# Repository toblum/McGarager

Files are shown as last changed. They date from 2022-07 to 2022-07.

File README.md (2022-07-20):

# McGarager v2
Simple MQTT garage door opener with endstop detection (reed sensor)

This is a rewrite of the initial McGarager firmware. It fits to the McGarager PCB.

It uses:
- The [prampec/IotWebConf@^3.2.1](https://github.com/prampec/IotWebConf) framework for easy setup, captive portal, config UI and OTA firmware upload.
- [knolleary/PubSubClient@^2.8](https://github.com/knolleary/pubsubclien) for MQTT communication
- [yiannisbourkelis/Uptime Librar@^1.0.0](https://github.com/YiannisBourkelis/Uptime-Library) for easy uptime display
- [Platformio](https://platformio.org/) for the build process.

Notes:
- No support for neopixel as of now.

Initial config values:
- AP SSID: McGarager / GaragerMc
- Config-UI credentials: admin / GaragerM
- Base MQTT topic: mc_garager

MQTT topics:
- #Base MQTT topic#/status: McGarager publishes JSON status messages to this topic when open/close inputs have changed of if trigged via command.
- #Base MQTT topic#/cmnd:   
  Topic that receives commands
    - Message "status": Trigger sending of status message.
    - Message "trigger": Make the relay close for 250 ms.

## PCB v1.0

- [Gerber files](assets/PCB/Gerber_PCB.zip)
- [BOM](assets/PCB/BOM_PCB_2022-07-20.csv)
- [Schematic](assets/PCB/Schematic_McGarager_2022-07-20.pdf)
- [Front](assets/PCB/PCB_PCB_2022-07-20_front.pdf)
- [Back](assets/PCB/PCB_PCB_2022-07-20_back.pdf)

Preview:
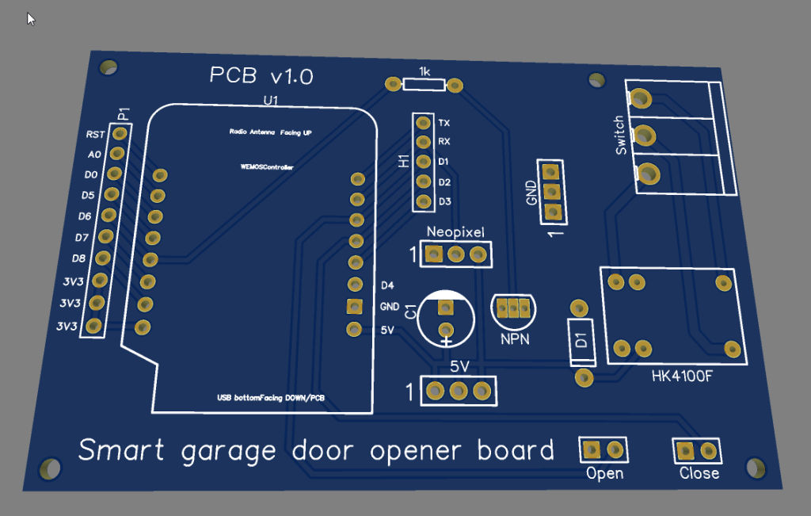
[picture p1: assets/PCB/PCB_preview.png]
PCB Preview


Front:
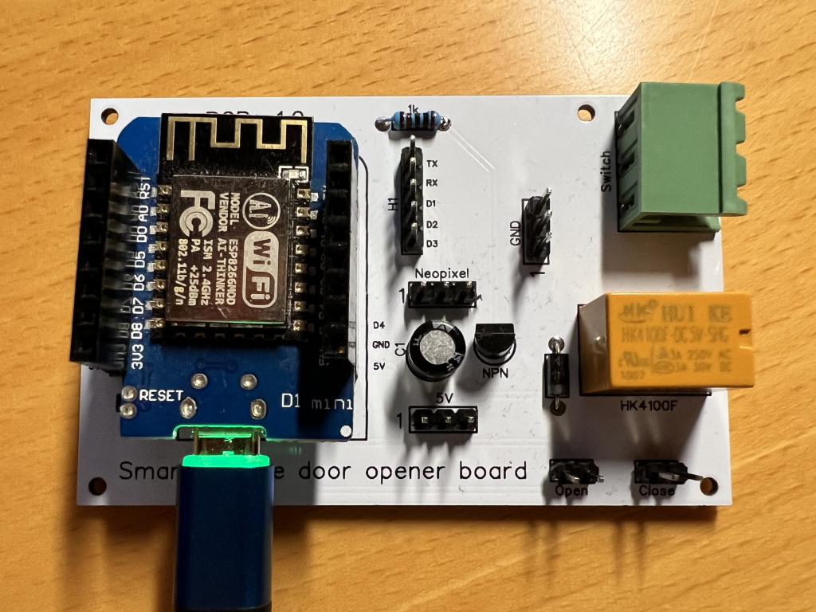
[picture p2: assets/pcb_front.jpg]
PCB front


Back:
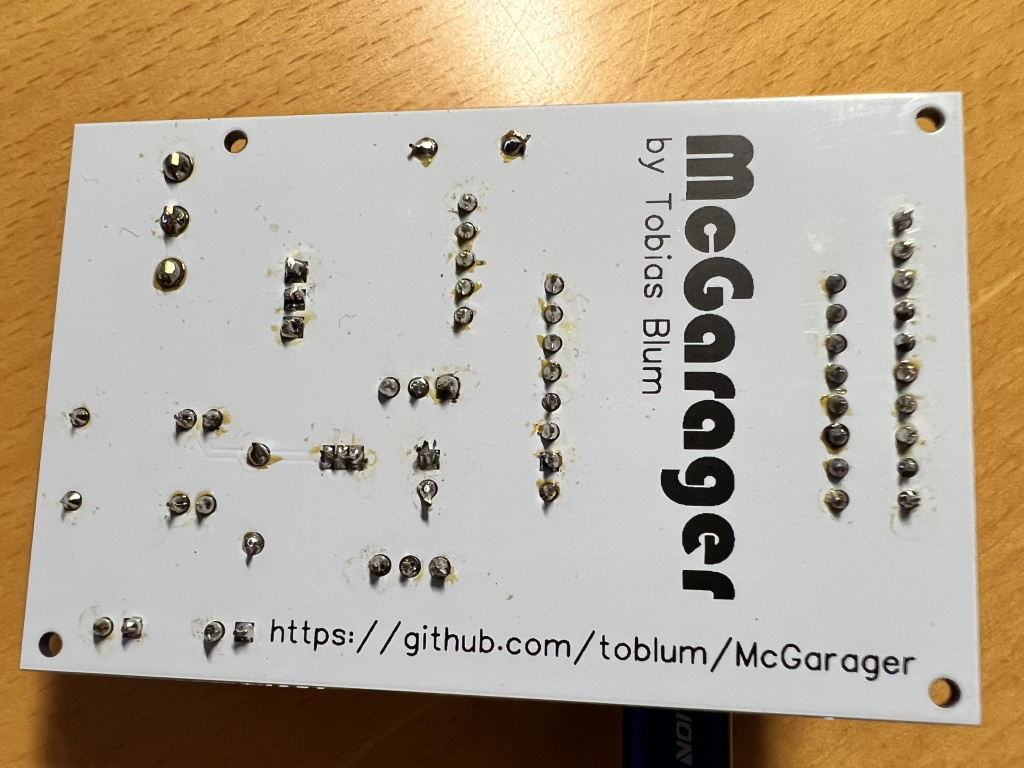
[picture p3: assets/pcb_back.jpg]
PCB back


## 3D printed enclosure

- [STL Case](assets/McGarager_enclosure_case.stl)
- [STL Lid](assets/McGarager_enclosure_lid.stl)

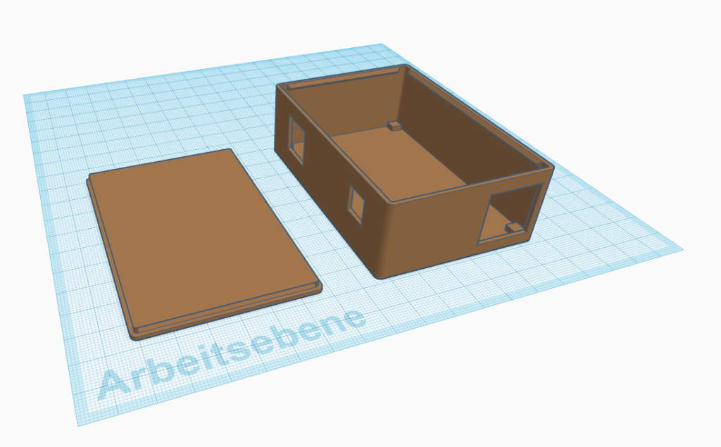
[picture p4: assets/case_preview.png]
Csae preview


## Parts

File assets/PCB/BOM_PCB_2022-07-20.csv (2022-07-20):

ID | Name | Designator | Footprint | Quantity | Manufacturer Part | Manufacturer | Supplier | Supplier Part | Price | Pins
1 | CAP-D6.3XF2.5 | C1 | CAP-D6.3XF2.5 | 1 |  |  |  |  |  | 2
2 | U1_D2 | Close | HDR1X2 | 1 |  |  |  |  |  | 2
3 | HDR1X2 | Open | HDR1X2 | 1 |  |  |  |  |  | 2
4 | 2EDGR-5.08-3P | Switch | 2EDGR-5.08-3P | 1 |  |  |  |  |  | 3
5 | HK4100F-DC5V-SHG | HK4100F | HK4100F-DC5V-SHG | 1 |  |  |  |  |  | 6
6 | 1N4004 | D1 | DO-41 | 1 |  |  |  |  |  | 2
7 | WEMOS | U1 | WEMOS | 1 |  |  |  |  |  | 16
8 | HDR1X5 | H1 | HDR1X5 | 1 |  |  |  |  |  | 5
9 | 1k | 1k | AXIAL-0.3 | 1 |  |  |  |  |  | 2
10 | BC547BTA | NPN | TO-92-3L | 1 |  |  |  |  |  | 3
11 | Header 10 | P1 | HDR1X10 | 1 |  |  |  |  |  | 10
12 | HDR1x3 | GND,5V,Neopixel | HDR1X3 | 3 |  |  |  |  |  | 3

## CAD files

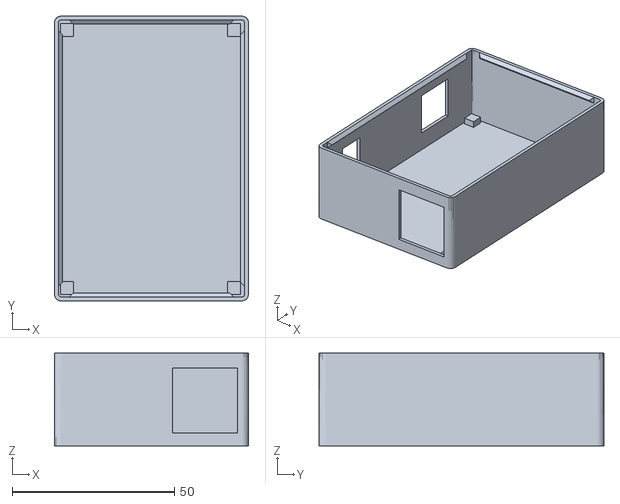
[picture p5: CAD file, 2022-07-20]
assets/McGarager_enclosure_case.stl
59.8 x 87.8 x 28.6

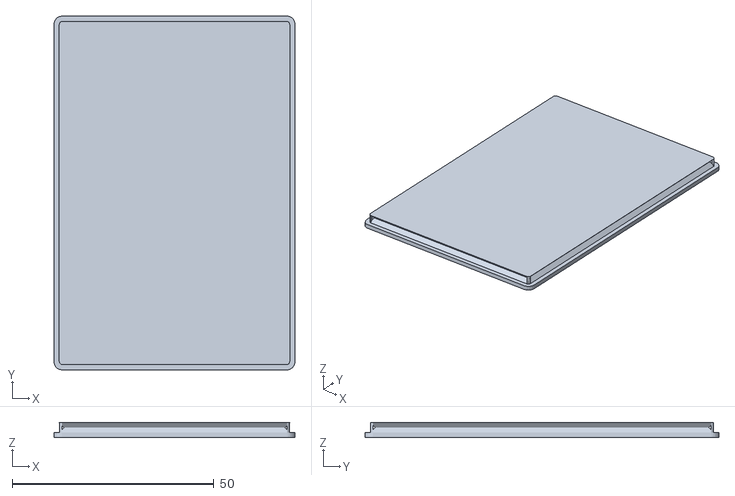
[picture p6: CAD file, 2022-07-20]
assets/McGarager_enclosure_lid.stl
59.8 x 87.8 x 3.60

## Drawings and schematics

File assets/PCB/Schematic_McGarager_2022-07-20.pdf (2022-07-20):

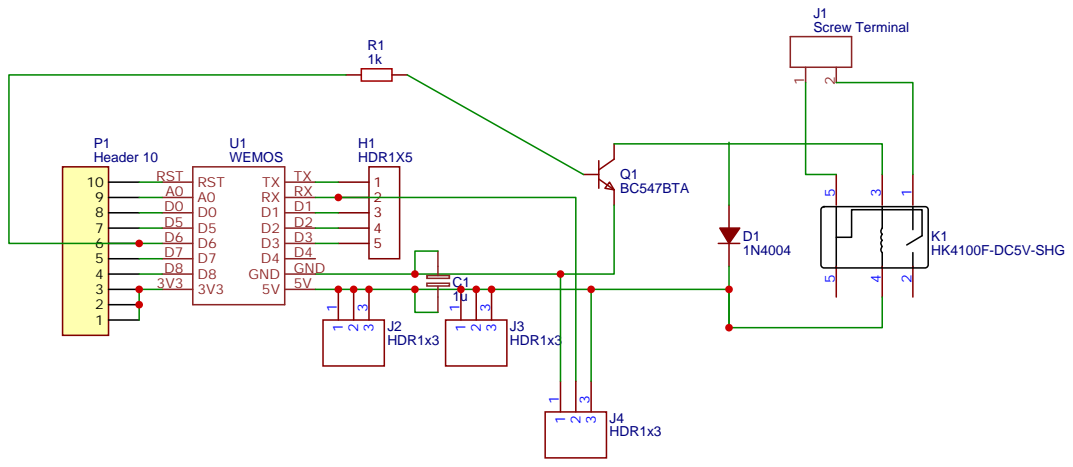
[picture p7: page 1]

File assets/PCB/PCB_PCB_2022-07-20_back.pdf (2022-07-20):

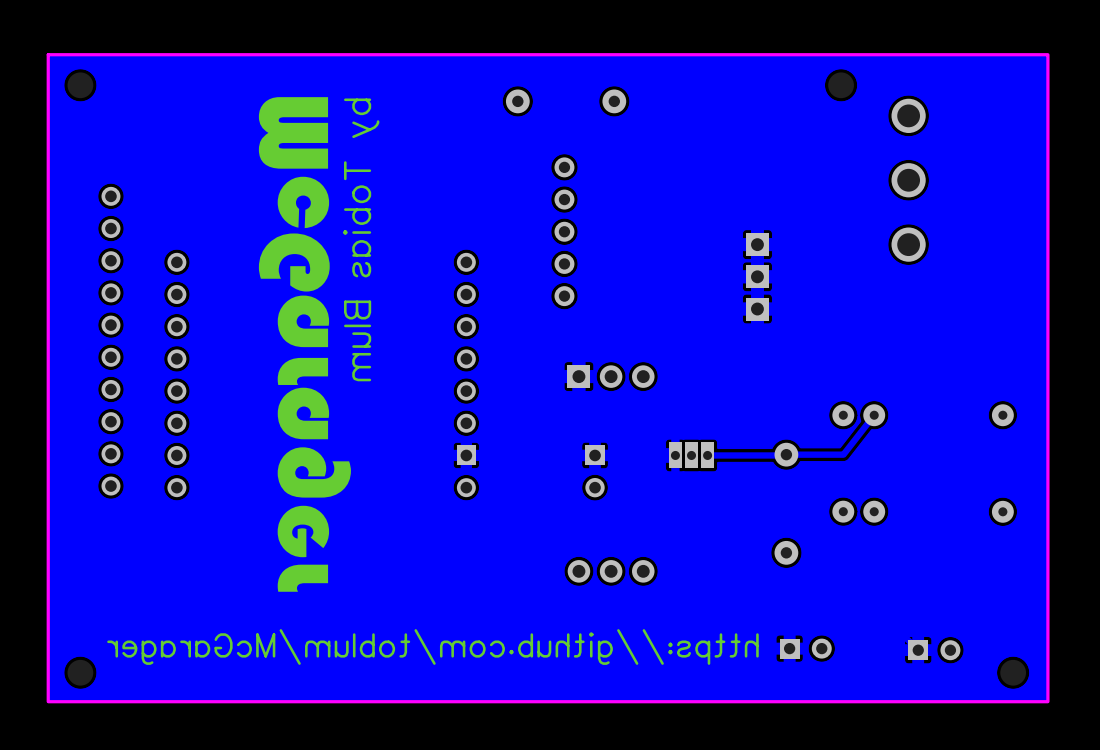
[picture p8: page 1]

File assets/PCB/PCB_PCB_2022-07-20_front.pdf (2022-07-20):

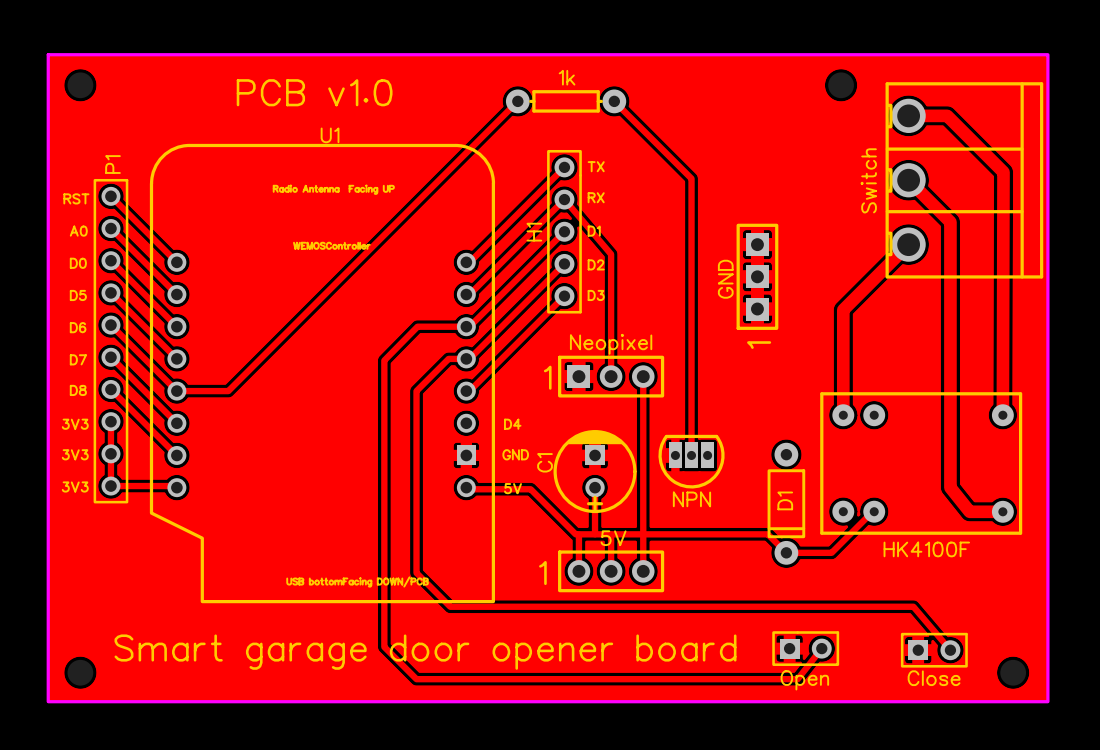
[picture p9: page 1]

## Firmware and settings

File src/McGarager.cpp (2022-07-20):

/**
 * McGarager.cpp -- Simple MQTT garage door opener with endstop detection (reed sensor)
 * https://github.com/toblum/McGarager
 *
 * Copyright (C) 2022 Tobias Blum <mcgarager@tobiasblum.de>
 *
 * This software may be modified and distributed under the terms
 * of the MIT license.  See the LICENSE file for details.
 */

#include <IotWebConf.h>
#include <IotWebConfUsing.h> // This loads aliases for easier class names.
#include <PubSubClient.h>
#include <uptime_formatter.h>
# include <ESP8266HTTPUpdateServer.h>

// -- Pins
#define RELAY_PIN 12
#define OPENED_SENSOR_PIN 5 // PIN 5 == D1
#define CLOSED_SENSOR_PIN 4 // PIN 4 == D2

bool sensorOpened = false;
bool sensorClosed = false;

// -- Initial name of the Thing. Used e.g. as SSID of the own Access Point.
const char thingName[] = "McGarager";

// -- Initial password to connect to the Thing, when it creates an own Access Point.
const char wifiInitialApPassword[] = "GaragerMc";

#define STRING_LEN 128
#define NUMBER_LEN 32

// -- Configuration specific key. The value should be modified if config structure was changed.
#define CONFIG_VERSION "mcg1"

// -- When CONFIG_PIN is pulled to ground on startup, the Thing will use the initial
//      password to buld an AP. (E.g. in case of lost password)
#define CONFIG_PIN D2

// -- Status indicator pin.
//      First it will light up (kept LOW), on Wifi connection it will blink,
//      when connected to the Wifi it will turn off (kept HIGH).
#define STATUS_PIN LED_BUILTIN

// -- Method declarations.
void handleRoot();
void configSaved();
bool formValidator(iotwebconf::WebRequestWrapper *webRequestWrapper);
IRAM_ATTR void handlePinChangeInterrupt();
void publishStatus();

DNSServer dnsServer;
WebServer server(80);
ESP8266HTTPUpdateServer httpUpdater;

// -- MQTT client setup
WiFiClient espClient;
PubSubClient mqttClient(espClient);
unsigned long lastMqttConnectionAttempt = 0;
unsigned long pinChangeDebounceTimeout = 0;
bool needsStatusUpdate = false;
bool connectMqtt();
void mqttCallback(char *topic, byte *payload, unsigned int length);

// -- IotWebConf setup
char mqttServerHostValue[STRING_LEN];
char mqttServerPortValue[NUMBER_LEN];
char mqttServerUserValue[STRING_LEN];
char mqttServerPassValue[STRING_LEN];
char mqttServerTopicValue[STRING_LEN];

IotWebConf iotWebConf(thingName, &dnsServer, &server, wifiInitialApPassword, CONFIG_VERSION);
IotWebConfTextParameter mqttServerHostParam = IotWebConfTextParameter("MQTT hostname", "mqttHost", mqttServerHostValue, STRING_LEN, "somehost.fritz.box");
IotWebConfNumberParameter mqttServerPortParam = IotWebConfNumberParameter("MQTT port", "mqttPort", mqttServerPortValue, NUMBER_LEN, "1883");
IotWebConfTextParameter mqttServerUserParam = IotWebConfTextParameter("MQTT username", "mqttUser", mqttServerUserValue, STRING_LEN);
IotWebConfTextParameter mqttServerPassParam = IotWebConfTextParameter("MQTT password", "mqttPass", mqttServerPassValue, STRING_LEN);
IotWebConfTextParameter mqttServerTopicParam = IotWebConfTextParameter("MQTT topic", "mqttTopic", mqttServerTopicValue, STRING_LEN, "mc_garager");
IotWebConfParameterGroup group1 = IotWebConfParameterGroup("groupMQTT", "MQTT");

// *************************************
// * setup()
// *************************************
void setup()
{
	Serial.begin(115200);
	Serial.println();
	Serial.println("Starting up...");

	pinMode(RELAY_PIN, OUTPUT);
	pinMode(OPENED_SENSOR_PIN, INPUT_PULLUP);
	pinMode(CLOSED_SENSOR_PIN, INPUT_PULLUP);

	attachInterrupt(digitalPinToInterrupt(OPENED_SENSOR_PIN), handlePinChangeInterrupt, CHANGE);
	attachInterrupt(digitalPinToInterrupt(CLOSED_SENSOR_PIN), handlePinChangeInterrupt, CHANGE);

	group1.addItem(&mqttServerHostParam);
	group1.addItem(&mqttServerPortParam);
	group1.addItem(&mqttServerUserParam);
	group1.addItem(&mqttServerPassParam);
	group1.addItem(&mqttServerTopicParam);

	iotWebConf.setStatusPin(STATUS_PIN);
	iotWebConf.setConfigPin(CONFIG_PIN);
	// iotWebConf.addSystemParameter(&stringParam);
	iotWebConf.addParameterGroup(&group1);
	iotWebConf.setConfigSavedCallback(&configSaved);
	iotWebConf.setFormValidator(&formValidator);
	iotWebConf.getApTimeoutParameter()->visible = true;

	iotWebConf.setupUpdateServer(
		[](const char *updatePath)
		{ httpUpdater.setup(&server, updatePath); },
		[](const char *userName, char *password)
		{ httpUpdater.updateCredentials(userName, password); });

	// -- Initializing the configuration.
	iotWebConf.init();

	// -- Set up required URL handlers on the web server.
	server.on("/", handleRoot);
	server.on("/config", []
			  { iotWebConf.handleConfig(); });
	server.onNotFound([]()
					  { iotWebConf.handleNotFound(); });

	// -- MQTT setup
	mqttClient.setServer(mqttServerHostValue, (uint16_t)atoi(mqttServerPortValue));
	mqttClient.setCallback(mqttCallback);

	Serial.println("setup() ready :-)");
}

// *************************************
// * loop()
// *************************************
void loop()
{
	// -- doLoop should be called as frequently as possible.
	iotWebConf.doLoop();
	mqttClient.loop();

	if ((iotWebConf.getState() == iotwebconf::OnLine) && (!mqttClient.connected()))
	{
		Serial.println("MQTT (re-)connect");
		connectMqtt();
	}

	if (needsStatusUpdate && pinChangeDebounceTimeout < millis()) {
		publishStatus();
		needsStatusUpdate = false;
	}
}

/**
 * Interrupt: Pin (open/closed state) changed
 */
IRAM_ATTR void handlePinChangeInterrupt() { 
    Serial.println("Interrupt Detected");
	pinChangeDebounceTimeout = millis() + 1000;
	needsStatusUpdate = true;
}

/**
 * Relay: Pulse relay
 */
void pulseRelay()
{
	digitalWrite(RELAY_PIN, HIGH);
	delay(250);
	digitalWrite(RELAY_PIN, LOW);
}

/**
 * Helper: Update sensor state
 */
void updateSensorState()
{
	sensorOpened = (digitalRead(OPENED_SENSOR_PIN) == LOW);
	sensorClosed = (digitalRead(CLOSED_SENSOR_PIN) == LOW);
}

/**
 * Publish status message via MQTT
 */
void publishStatus()
{
	updateSensorState();

	String opened = (sensorOpened) ? "true" : "false";
	String closed = (sensorClosed) ? "true" : "false";
	long rssi = WiFi.RSSI();
	String status = "{\"rssi\" : \"" + String(rssi) + "\", \"memory\" : \"" + String(ESP.getFreeHeap()) + "\", \"uptime\" : \"" + uptime_formatter::getUptime() + "\", \"sensor_opened\" : \"" + opened + "\", \"sensor_closed\" : \"" + closed + "\"}";
	// Serial.println(status);

	char message_buff[256];
	status.toCharArray(message_buff, status.length() + 1);

	char topicStatus[STRING_LEN + 7];
	sprintf(topicStatus, "%s/status", mqttServerTopicValue);
	mqttClient.publish(topicStatus, message_buff);
}

/**
 * (Re-)connect to MQTT broker
 */
bool connectMqtt()
{
	unsigned long now = millis();
	if (5000 > now - lastMqttConnectionAttempt)
	{
		// Do not repeat within 5 sec.
		return false;
	}
	Serial.println("Connecting to MQTT server...");

	String clientId = "McGaragerClient-";
	clientId += String(random(0xffff), HEX);

	if (mqttClient.connect(clientId.c_str()))
	{
		Serial.println("Connected!");

		char topicCmnd[STRING_LEN + 5];
		sprintf(topicCmnd, "%s/cmnd", mqttServerTopicValue);

		mqttClient.subscribe(topicCmnd);
		return true;
	}
	else
	{
		Serial.print("MQTT connection failed, rc=");
		Serial.print(mqttClient.state());
		Serial.println(" try again in 5 seconds");
		lastMqttConnectionAttempt = now;
		return false;
	}
}

/**
 * Callback on MQTT message
 */
void mqttCallback(char *topic, byte *payload, unsigned int length)
{
	Serial.print("Message arrived [");
	Serial.print(topic);
	Serial.print("] ");
	for (unsigned int i = 0; i < length; i++)
	{
		Serial.print((char)payload[i]);
	}
	Serial.println();

	if (!strncmp((char *)payload, "trigger", length))
	{
		Serial.println("Received trigger");
		pulseRelay();
	}
	if (!strncmp((char *)payload, "status", length))
	{
		Serial.println("Received status");
		needsStatusUpdate = true;
	}
}

/**
 * Handle web requests to "/" path.
 */
void handleRoot()
{
	// -- Let IotWebConf test and handle captive portal requests.
	if (iotWebConf.handleCaptivePortal())
	{
		// -- Captive portal request were already served.
		return;
	}

	String s = "<!DOCTYPE html><html lang=\"en\"><head><meta name=\"viewport\" content=\"width=device-width, initial-scale=1, user-scalable=no\"/>";
	s += "<title>McGarager v2</title></head><body style=\"font-family:Arial;\"><h1>McGarager v2</h1>";
	s += "<ul>";
	s += "<li>MQTT hostname: ";
	s += mqttServerHostValue;
	s += "<li>MQTT port: ";
	s += atoi(mqttServerPortValue);
	s += "<li>MQTT username: ";
	s += mqttServerUserValue;
	s += "<li>MQTT password: ";
	s += mqttServerPassValue;
	s += "<li>MQTT topic: ";
	s += mqttServerTopicValue;
	s += "<li>Uptime: ";
	s += uptime_formatter::getUptime();
	s += "<li>Free memory: ";
	s += String(ESP.getFreeHeap());
	s += " Bytes";

	s += "</ul>";
	s += "<p>Go to <a href='config'>configure page</a> to change values.</p>";
	s += "<p>GitHub: <a href='https://github.com/toblum/McGarager' target='_blank'>https://github.com/toblum/McGarager</a></p>";
	s += "</body></html>\n";

	server.send(200, "text/html", s);
}

/**
 * Callback when IotWebConf config is saved.
 */
void configSaved()
{
	Serial.println("Configuration was updated.");
}

/**
 * Callback for IotWebConf config validation.
 */
bool formValidator(iotwebconf::WebRequestWrapper *webRequestWrapper)
{
	Serial.println("Validating form.");
	bool valid = true;

	/*
	  int l = webRequestWrapper->arg(stringParam.getId()).length();
	  if (l < 3)
	  {
		stringParam.errorMessage = "Please provide at least 3 characters for this test!";
		valid = false;
	  }
	*/
	return valid;
}

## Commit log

2022-07-20 Check to pin interrupts and publish status message
2022-07-20 Debounce sensor
